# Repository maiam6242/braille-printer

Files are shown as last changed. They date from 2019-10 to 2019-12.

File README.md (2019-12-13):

# Portabraille Printer by Team Dot Dot Dot

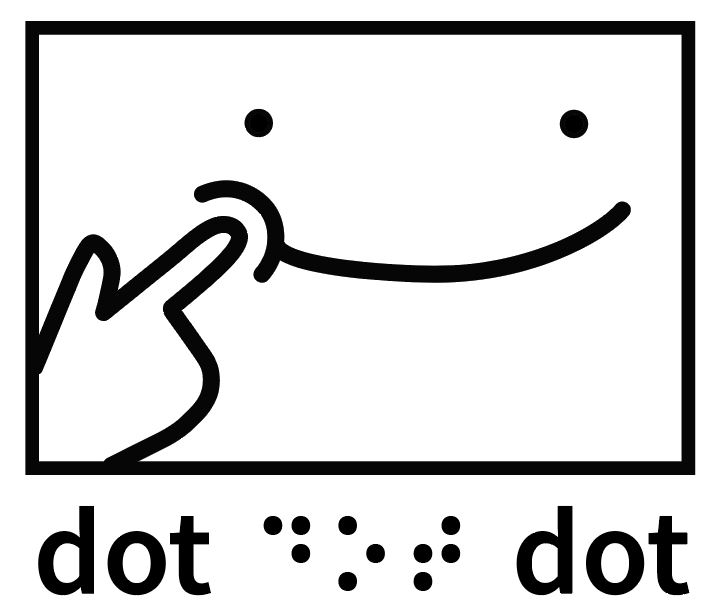
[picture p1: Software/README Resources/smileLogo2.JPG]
Team dot dot dot logo


### The Portabraille Printer is a portable and accessible braille printer which enables users who are visually impaired to quickly and easily produce accurate, high quality braille.

## Table of Contents
- [Introduction](#Introduction "Introduction")
- [This Repository](#This-Repository "This Repository") 
- [Requirements](#Requirements "Requirements")
- [Installation](#Installation "Installation")  
- [Feedback](#Feedback "Feedback") 
- [Team](#Team "Team")  
- [Acknowledgments](#Acknowledgments "Acknowledgments") 

## Introduction
The Portabraille Printer is a device that takes in an English text input, translates that text into uncontracted braille, then prints said braille text on braille paper. It is a low cost product that aims to allow people who are visually impaired to create braille quickly, with applications ranging from producing quick meeting notes to creating accessible promotional materials on the fly. The printer is light, with handles for easy transportation, and has an easy-to-use interface with both braille and English text, creating a user friendly experience for those who are visually impaired or blind. Text documents can be fed to the printer via either the Portabraille Portal on the Portabraille Network or by plugging in a USB. 

## This Repository

This repository contains the vast majority of the files which we created over the course of this project. It is split into two main folders: [Software](https://github.com/maiam6242/braille-printer/tree/master/Software "Software Forlder") and [Firmware](https://github.com/maiam6242/braille-printer/tree/master/Firmware "Firmware Folder"), each of which houses artifacts for the respective subsystems. These folders are also split into multiple subfolders. There is also a [Branding](https://github.com/maiam6242/braille-printer/tree/master/Branding "Branding Folder") folder which has the logo that we used on our shirts.

On the software side, the [Text Side Folder](https://github.com/maiam6242/braille-printer/tree/master/Software/Text%20Side "Text Side Folder") has software that takes a text input, converts it to a braille output and sends it to the firmware. All of this is written in Python. The [Physical Interface Folder](https://github.com/maiam6242/braille-printer/tree/master/Software/Physical%20Interface "Physical Interface Folder") contains software written in Python and designs created in Illustrator which relate to the user interface on our printer. The web interface written in html and designed in Illustrator is in the [Web Interface Folder](https://github.com/maiam6242/braille-printer/tree/master/Software/Web%20Interface "Web Interface Folder"). The [Recognizing Input Folder](https://github.com/maiam6242/braille-printer/tree/master/Software/Recognizing%20Input) includes all of the scripts in bash and Python that allow us to take in USB or Wifi input and the [README Resources Folder](https://github.com/maiam6242/braille-printer/tree/master/Software/README%20Resources "README Resources Folder") contains all of the files referenced in this document. Lastly, the [Startup Scripts Folder](https://github.com/maiam6242/braille-printer/tree/master/Software/StartupScripts "Startup Scripts Folder") contains the scripts which need to be run on the Raspberry Pi to ensure that our software and network run on startup. 

In the firmware folder, the firmware that controls the way paper is loaded and how solenoids act is in the [Arduino Firmware Folder](https://github.com/maiam6242/braille-printer/tree/master/Firmware/Arduino%20Firmware "Arduino Firmware Folder"). All of our firmware is written in C++. The [PCB Folder](https://github.com/maiam6242/braille-printer/tree/master/Firmware/PCB "PCB Folder") contains all of the artifacts from our PCB design.

## Requirements

- Python 3 (or newer)
- Raspberry Pi 3B, 3B+ or 4
- Rasbian Jesse (or newer)

## Installation
The software that runs on the Portabraille Printer has a variety of dependencies. The [startup bash script](https://github.com/maiam6242/braille-printer/blob/master/startup.bash "Startup Bash Script") automatically installs all of the dependencies from all components of our firmware and software. Instructions and code samples for installing these dependencies individually are below. 

#### Python Text to Speech
The following bash command installs pyttsx3, a text to speech library for Python. 
``` bash
pip3 install pyttsx3
```

#### NumPy
The following bash command installs NumPy, a package for computing with Python. 
``` bash
pip3 install numpy
```

#### GPIO Zero
The following bash command installs GPIO Zero, a library for interfacing GPIO devices with Raspberry Pi.
``` bash
pip3 install gpiozero
```

#### PySerial
The following bash command installs pySerial, a module for accessing the serial port.
``` bash
pip3 install pyserial
```

#### eSpeak
The following bash command installs eSpeak, an open source speech synthesizer for Linux and Windows.
```bash
sudo apt-get install espeak
```

#### Flask
The following bash command installs Flask, a microweb framework.
```bash
pip3 install Flask
```

## Feedback
We would love to hear feedback on this project! Feel free to [email us](mailto:mmaterman@olin.edu "mmaterman@olin.edu") or [submit an issue](https://github.com/maiam6242/braille-printer/issues/new/choose "New Issue Request"). If you are interested in contributing to this project or chatting about it in general, please don't hesitate to [email us](mailto:mmaterman@olin.edu "mmaterman@olin.edu") here!

## Team
Annie Tor [@ator1](https://github.com/ator1 "Annie's GitHub")   
Colin Snow [@colinmsnow](https://github.com/colinmsnow "Colin's GitHub")  
Maia Materman [@maiam6242](https://github.com/maiam6242 "Maia's GitHub")  
Megan Ku [@megku4u](https://github.com/megku4u "Megan's GitHub")  
Nathan Weil [@NWeil](https://github.com/NWeil "Nathan's GitHub")  

## Acknowledgments
Thanks to the Fall 2019 Principles of Engineering Teaching Team, Professors Aaron Hoover, Amon Millner, Siddhartan Govindasamy and Stan Reifel for their support and assistance throughout this process. Additional thanks to Frank Ventura, Jerry Berrier, David Kingsbury, John Smith, and Jeanette Kutash and for their INDISPENSABLE help during this adventure. The insights they provided about our design helped us craft a product that is actually usable. Lastly, thank you to the MIT Visually Impaired and Blind User Group for hosting us and letting us pick their brains regarding our printer and braille in general.

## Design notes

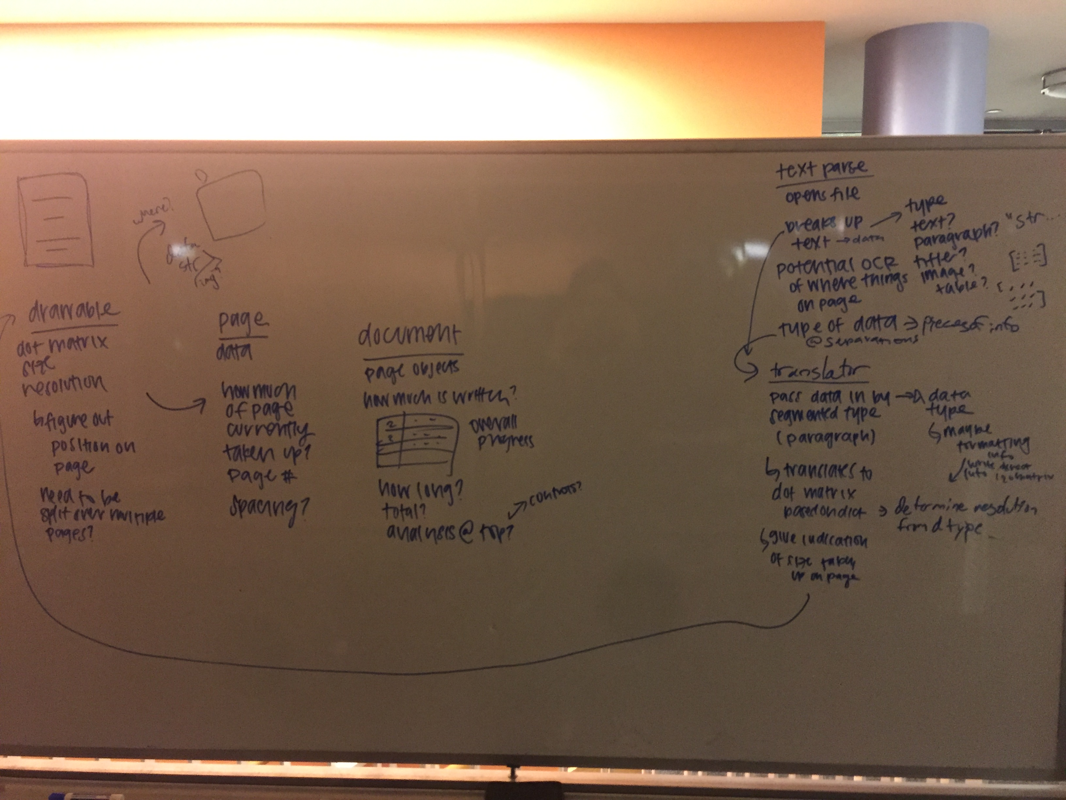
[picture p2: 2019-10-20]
Software/Text_Side/Sprint 1 Inital Code Brainstorm.JPG

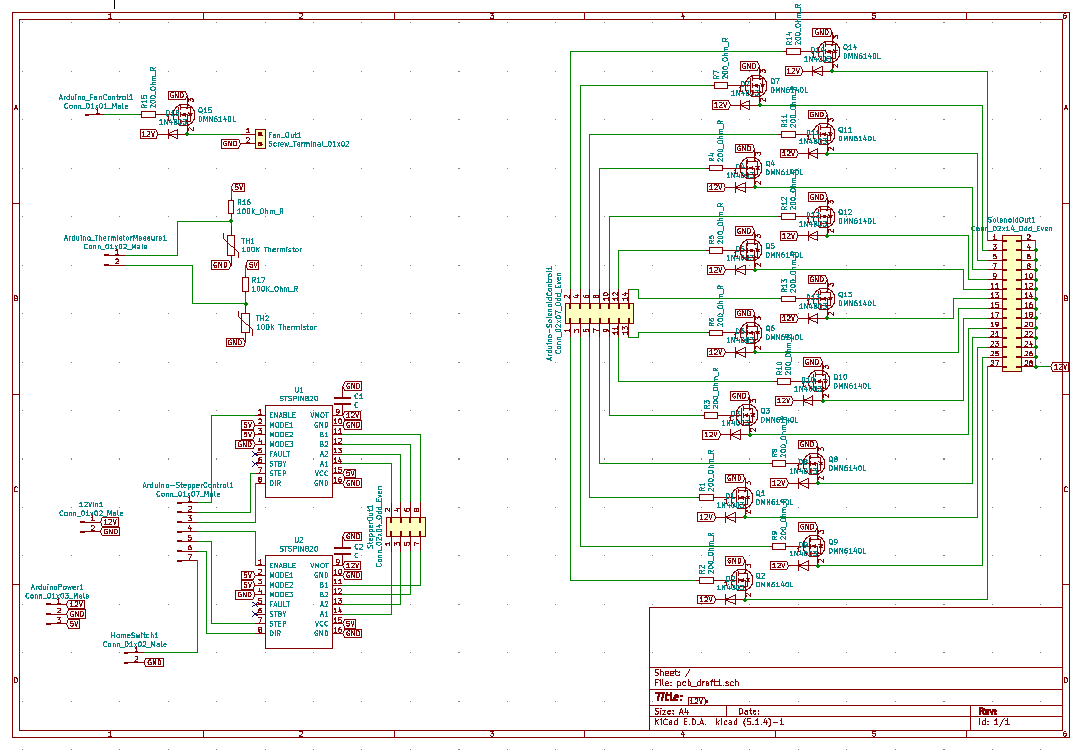
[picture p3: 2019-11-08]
Firmware/PCB/draft1.PNG

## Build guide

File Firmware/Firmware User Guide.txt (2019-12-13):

Firmware User Guide
This guide is intended to describe how the braille firmware works and how it can be used to perform advanced actions.

Overview

The system is built to closely resemble the Gcode standard and shares many common commands with 3D printers. Instructions are sent over serial to the Arduino in the form of a string followed by “\n”. Each command specifies a single action or set of actions for the printer to execute. All commands are currently set to be blocking, which means that the program will not listen for another command until the first command finishes. The program returns information about its interpretation of the command and the resulting action over serial, but this can be disabled with the command M21, which makes it simply return 0 when the last command is completed.

Commands

Movement:

Stepper movement currently operates on a “go-to character” function which assumes that the braille characters are a constant width. They are not a constant width, so that needs to be changed either in the firmware or in python, but it is not really a pressing issue. Movement is split into x and y dimensions, where x is along the width of the paper and y is along its length. There are two commands for movement, G0, and G1, with the only difference being that G1 is half of the speed of G0. They work as follows:

        G0 (axis) (value)  Move the (axis) to the character (value)
                Ex. G0 x 12 moves the x axis to the 12th character
                Ex. G0 y 4 moves the y axis to the fourth character

        G1 (axis) (value)  Same as G0 but at half speed

Solenoids:

The solenoids are controlled with the F command, which takes a sequence of 1s and 0s to denote which solenoid is fired. There is no established order for which solenoid goes where yet so you can decide however you want. The command looks like this:

        F (values[14])  Fire the solenoids with a value of 1
                Ex. F 11111111111111 fires all solenoids
                Ex. F 10000000000000 fires only the first solenoid

Other commands:

There are also a variety of other commands, most of which are made up of the above, to perform other important functions. Steppers should be enabled at the beginning of the program and disabled at the end, and paper loading and x-axis homing should occur for each sheet. For command from Python M21 should be run before all other commands so that the output is consistent. They are as follows:

        G28                     Home (x) axis
        M17                     Enable all steppers
        M18                     Disable all steppers
        M701                    Load paper
        M702                    Unload paper
        M21                     Toggle machine-read mode

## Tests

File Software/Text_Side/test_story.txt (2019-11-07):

Title

“Why in the world do you walk sideways like that?” said a Mother Crab to her son. “You should always walk straight forward with your toes turned out.”

“Show me how to walk, mother dear,” answered the little Crab obediently, “I want to learn.”

So the old Crab tried and tried to walk straight forward. But she could walk sideways only, like her son. And when she wanted to turn her toes out she tripped and fell on her nose.

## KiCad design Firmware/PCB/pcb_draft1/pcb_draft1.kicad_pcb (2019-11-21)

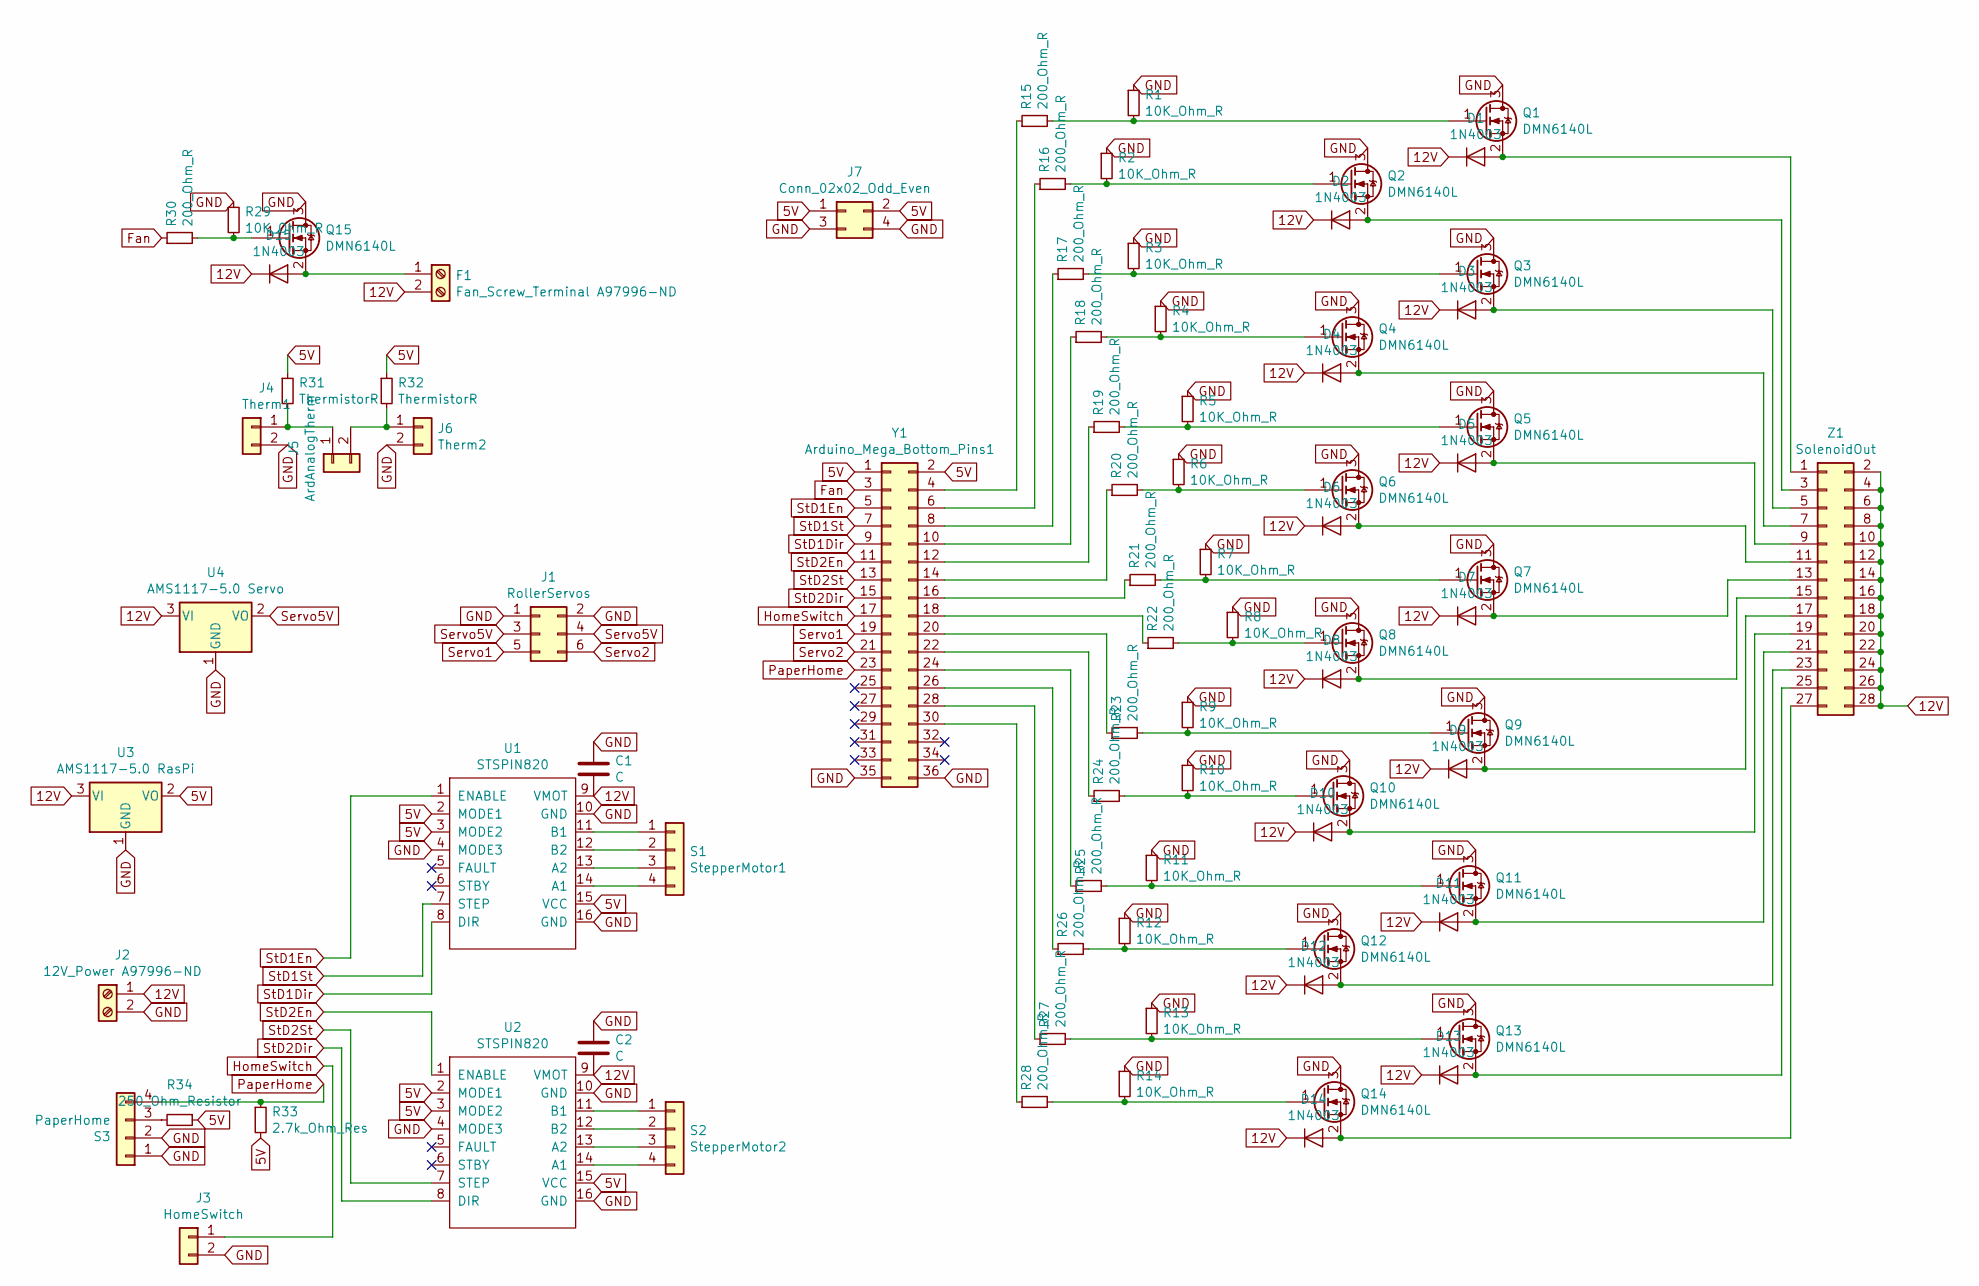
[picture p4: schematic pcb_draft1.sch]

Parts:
C1, C2: C; CP_Radial_D8.0mm_P3.50mm
D1, D2, D3, D4, D5, D6, D7, D8, D9, D10, D11, D12, D13, D14, D15: 1N4003; D_DO-41_SOD81_P10.16mm_Horizontal
F1: Fan_Screw_Terminal A97996-ND; TerminalBlock_Phoenix_MKDS-1,5-2_1x02_P5.00mm_Horizontal
J1: RollerServos; PinHeader_2x03_P2.54mm_Vertical
J2: 12V_Power A97996-ND; TerminalBlock_Phoenix_MKDS-1,5-2_1x02_P5.00mm_Horizontal
J3: HomeSwitch; PinHeader_1x02_P2.54mm_Vertical
J4: Therm1; PinHeader_1x02_P2.54mm_Vertical
J5: ArdAnalogTherm; PinHeader_1x02_P2.54mm_Vertical
J6: Therm2; PinHeader_1x02_P2.54mm_Vertical
J7: Conn_02x02_Odd_Even; PinHeader_2x02_P2.54mm_Vertical
Q1, Q2, Q3, Q4, Q5, Q6, Q7, Q8, Q9, Q10, Q11, Q12, Q13, Q14, Q15: DMN6140L; SOT-223-edited
R1, R2, R3, R4, R5, R6, R7, R8, R9, R10, R11, R12, R13, R14, R29: 10K_Ohm_R; R_0402_1005Metric
R15, R16, R17, R18, R19, R20, R21, R22, R23, R24, R25, R26, R27, R28, R30: 200_Ohm_R; R_0603_1608Metric
R31, R32: ThermistorR; PinHeader_1x02_P2.54mm_Vertical
R33: 2.7k_Ohm_Res; R_0402_1005Metric
R34: 250_Ohm_Resistor; R_0603_1608Metric
S1: StepperMotor1; PinHeader_1x04_P2.54mm_Vertical
S2: StepperMotor2; PinHeader_1x04_P2.54mm_Vertical
S3: PaperHome; PinHeader_1x04_P2.54mm_Vertical
U1, U2: STSPIN820; stepper_driver
U3: AMS1117-5.0 RasPi; SOT-223-3_TabPin2
U4: AMS1117-5.0 Servo; SOT-223-3_TabPin2
Y1: Arduino_Mega_Bottom_Pins1; PinHeader_2x18_P2.54mm_Vertical
Z1: SolenoidOut; PinHeader_2x14_P2.54mm_Vertical

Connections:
5V: J7.1, J7.2, R31.1, R32.1, R33.2, R34.1, U1.2 (MODE1), U1.3 (MODE2), U1.15 (VCC), U2.2 (MODE1), U2.3 (MODE2), U2.15 (VCC), U3.2 (VO), Y1.1, Y1.2
12V: C1.2, C2.2, D1.1 (K), D2.1 (K), D3.1 (K), D4.1 (K), D5.1 (K), D6.1 (K), D7.1 (K), D8.1 (K), D9.1 (K), D10.1 (K), D11.1 (K), D12.1 (K), D13.1 (K), D14.1 (K), D15.1 (K), F1.2, J2.1, U1.9 (VMOT), U2.9 (VMOT), U3.3 (VI), U4.3 (VI), Z1.2, Z1.4, Z1.6, Z1.8, Z1.10, Z1.12, Z1.14, Z1.16, Z1.18, Z1.20, Z1.22, Z1.24, Z1.26, Z1.28
Fan: R30.1, Y1.3
GND: C1.1, C2.1, J1.1, J1.2, J2.2, J3.2, J4.2, J6.2, J7.3, J7.4, Q1.3 (D), Q2.3 (D), Q3.3 (D), Q4.3 (D), Q5.3 (D), Q6.3 (D), Q7.3 (D), Q8.3 (D), Q9.3 (D), Q10.3 (D), Q11.3 (D), Q12.3 (D), Q13.3 (D), Q14.3 (D), Q15.3 (D), R1.1, R2.1, R3.1, R4.1, R5.1, R6.1, R7.1, R8.1, R9.1, R10.1, R11.1, R12.1, R13.1, R14.1, R29.1, S3.1, S3.2, U1.4 (MODE3), U1.10 (GND), U1.16 (GND), U2.4 (MODE3), U2.10 (GND), U2.16 (GND), U3.1 (GND), U4.1 (GND), Y1.35, Y1.36
HomeSwitch: J3.1, Y1.17
unnamed: D1.2 (A), Q1.2 (S), Z1.1
unnamed: D2.2 (A), Q2.2 (S), Z1.3
unnamed: D3.2 (A), Q3.2 (S), Z1.5
unnamed: D4.2 (A), Q4.2 (S), Z1.7
unnamed: D5.2 (A), Q5.2 (S), Z1.9
unnamed: D6.2 (A), Q6.2 (S), Z1.11
unnamed: D7.2 (A), Q7.2 (S), Z1.13
unnamed: D8.2 (A), Q8.2 (S), Z1.15
unnamed: D9.2 (A), Q9.2 (S), Z1.17
unnamed: D10.2 (A), Q10.2 (S), Z1.19
unnamed: D11.2 (A), Q11.2 (S), Z1.21
unnamed: D12.2 (A), Q12.2 (S), Z1.23
unnamed: D13.2 (A), Q13.2 (S), Z1.25
unnamed: D14.2 (A), Q14.2 (S), Z1.27
unnamed: D15.2 (A), F1.1, Q15.2 (S)
unnamed: J4.1, J5.1, R31.2
unnamed: J5.2, J6.1, R32.2
unnamed: Q1.1 (G), R1.2, R15.2
unnamed: Q2.1 (G), R2.2, R16.2
unnamed: Q3.1 (G), R3.2, R17.2
unnamed: Q4.1 (G), R4.2, R18.2
unnamed: Q5.1 (G), R5.2, R19.2
unnamed: Q6.1 (G), R6.2, R20.2
unnamed: Q7.1 (G), R7.2, R21.2
unnamed: Q8.1 (G), R8.2, R22.2
unnamed: Q9.1 (G), R9.2, R23.2
unnamed: Q10.1 (G), R10.2, R24.2
unnamed: Q11.1 (G), R11.2, R25.2
unnamed: Q12.1 (G), R12.2, R26.2
unnamed: Q13.1 (G), R13.2, R27.2
unnamed: Q14.1 (G), R14.2, R28.2
unnamed: Q15.1 (G), R29.2, R30.2
unnamed: R15.1, Y1.4
unnamed: R16.1, Y1.6
unnamed: R17.1, Y1.8
unnamed: R18.1, Y1.10
unnamed: R19.1, Y1.12
unnamed: R20.1, Y1.14
unnamed: R21.1, Y1.16
unnamed: R22.1, Y1.18
unnamed: R23.1, Y1.20
unnamed: R24.1, Y1.22
unnamed: R25.1, Y1.24
unnamed: R26.1, Y1.26
unnamed: R27.1, Y1.28
unnamed: R28.1, Y1.30
unnamed: R34.2, S3.3
unnamed: S1.1, U1.11 (B1)
unnamed: S1.2, U1.12 (B2)
unnamed: S1.3, U1.13 (A2)
unnamed: S1.4, U1.14 (A1)
unnamed: S2.1, U2.11 (B1)
unnamed: S2.2, U2.12 (B2)
unnamed: S2.3, U2.13 (A2)
unnamed: S2.4, U2.14 (A1)
PaperHome: R33.1, S3.4, Y1.23
Servo1: J1.5, Y1.19
Servo2: J1.6, Y1.21
Servo5V: J1.3, J1.4, U4.2 (VO)
StD1Dir: U1.8 (DIR), Y1.9
StD1En: U1.1 (ENABLE), Y1.5
StD1St: U1.7 (STEP), Y1.7
StD2Dir: U2.8 (DIR), Y1.15
StD2En: U2.1 (ENABLE), Y1.11
StD2St: U2.7 (STEP), Y1.13

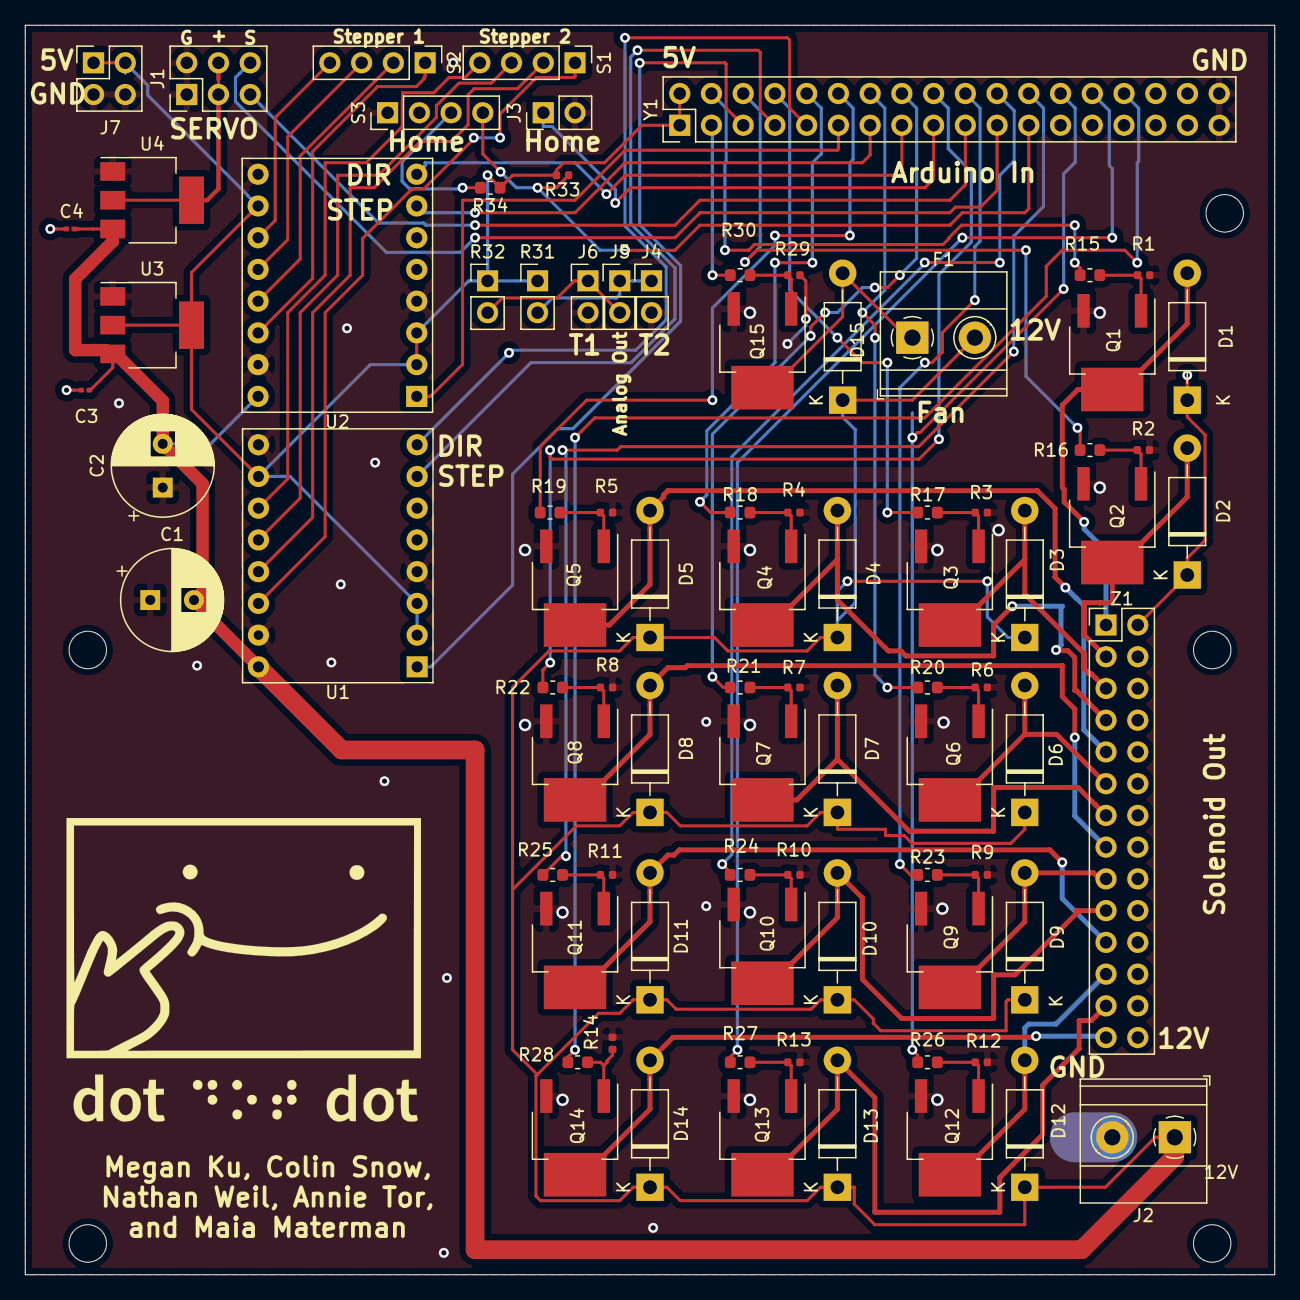
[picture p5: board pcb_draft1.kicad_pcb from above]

Board: 2 copper layers, 100.0 x 100.0 mm, 86 parts (0 on the bottom side), 70 nets.

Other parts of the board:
12V: MountingHole_3mm
C3, C4: C_0201_0603Metric

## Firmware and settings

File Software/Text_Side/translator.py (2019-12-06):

#coding=utf-8
'''Translates text into braille'''

import numpy as np
#TODO: Add single opening and closing quotation marks...
# also figure out if this is already done, oof


# page = page
CHARACTERS_PER_LINE = 28
SYMBOLS = {'a' : np.array([[1, 0], [0, 0], [0, 0]]),
           'b' : np.array([[1, 0], [1, 0], [0, 0]]),
           'c' : np.array([[1, 1], [0, 0], [0, 0]]),
           'd' : np.array([[1, 1], [0, 1], [0, 0]]),
           'e' : np.array([[1, 0], [0, 1], [0, 0]]),
           'f' : np.array([[1, 1], [1, 0], [0, 0]]),
           'g' : np.array([[1, 1], [1, 1], [0, 0]]),
           'h' : np.array([[1, 0], [1, 1], [0, 0]]),
           'i' : np.array([[0, 1], [1, 0], [0, 0]]),
           'j' : np.array([[0, 1], [1, 1], [0, 0]]),
           'k' : np.array([[1, 0], [0, 0], [1, 0]]),
           'l' : np.array([[1, 0], [1, 0], [1, 0]]),
           'm' : np.array([[1, 1], [0, 0], [1, 0]]),
           'n' : np.array([[1, 1], [0, 1], [1, 0]]),
           'o' : np.array([[1, 0], [0, 1], [1, 0]]),
           'p' : np.array([[1, 1], [1, 0], [1, 0]]),
           'q' : np.array([[1, 1], [1, 1], [1, 0]]),
           'r' : np.array([[1, 0], [1, 1], [1, 0]]),
           's' : np.array([[0, 1], [1, 0], [1, 0]]),
           't' : np.array([[0, 1], [1, 1], [1, 0]]),
           'u' : np.array([[1, 0], [0, 0], [1, 1]]),
           'v' : np.array([[1, 0], [1, 0], [1, 1]]),
           'w' : np.array([[0, 1], [1, 1], [0, 1]]),
           'x' : np.array([[1, 1], [0, 0], [1, 1]]),
           'y' : np.array([[1, 1], [0, 1], [1, 1]]),
           'z' : np.array([[1, 0], [0, 1], [1, 1]]),
           '1' : np.array([[1, 0], [0, 0], [0, 0]]),
           '2' : np.array([[1, 0], [1, 0], [0, 0]]),
           '3' : np.array([[1, 1], [0, 0], [0, 0]]),
           '4' : np.array([[1, 1], [0, 1], [0, 0]]),
           '5' : np.array([[1, 0], [0, 1], [0, 0]]),
           '6' : np.array([[1, 1], [1, 0], [0, 0]]),
           '7' : np.array([[1, 1], [1, 1], [0, 0]]),
           '8' : np.array([[1, 0], [1, 1], [0, 0]]),
           '9' : np.array([[0, 1], [1, 0], [0, 0]]),
           '0' : np.array([[0, 1], [1, 1], [0, 0]]),
           ' ' : np.array([[0, 0], [0, 0], [0, 0]]),
           ',' : np.array([[0, 0], [1, 0], [0, 0]]),
           ';' : np.array([[0, 0], [1, 0], [1, 0]]),
           ':' : np.array([[0, 0], [1, 1], [0, 0]]),
           '.' : np.array([[0, 0], [1, 1], [0, 1]]),
           '!' : np.array([[0, 0], [1, 1], [1, 0]]),
           "'" : np.array([[0, 0], [0, 0], [1, 0]]),
           '-' : np.array([[0, 0], [0, 0], [1, 1]]),
           '?' : np.array([[0, 0], [1, 0], [1, 1]]),
           '#' : np.array([[0, 1], [0, 1], [1, 1]]),
           '(' : np.array([[0, 0], [1, 1], [1, 1]]),
           ')' : np.array([[0, 0], [1, 1], [1, 1]]),
           'Ξ' : np.array([[0, 1], [0, 1], [1, 1]]),
           '“' : np.array([[0, 0], [1, 0], [1, 1]]),
           '”' : np.array([[0, 0], [0, 1], [1, 1]]),
           'opening "' : np.array([[0, 0], [1, 0], [1, 1]]),
           'closing "' : np.array([[0, 0], [0, 1], [1, 1]]),
           'ζ' : np.array([[0, 0], [0, 0], [0, 1]]),
           'η' : np.array([[0, 0, 0, 0], [0, 0, 0, 0],
                           [0, 1, 0, 1]]),
           '_' : np.array([[0, 1, 0, 0], [0, 0, 0, 0],
                           [0, 1, 1, 1]]),
           '[' : np.array([[0, 1, 1, 0], [0, 0, 1, 0],
                           [0, 1, 0, 1]]),
           ']' : np.array([[0, 1, 0, 1], [0, 0, 0, 1],
                           [0, 1, 1, 0]]),
           '*' : np.array([[0, 0, 0, 0], [0, 1, 0, 1],
                           [0, 0, 1, 0]]),
           '$' : np.array([[0, 1, 0, 1], [0, 0, 1, 0],
                           [0, 0, 1, 0]])
           }

class Translator:
    '''Translates text to braille'''

    def __init__(self, interface):
        self.interface = interface

    OPEN_QUOTE = False
    size = []

    def convert_to_braille(self, segment):
        '''
        Converts the entirety of the segment into a dot matrix based
        on the'SYMBOLS' dictionary in this class
        Args: the whole segment in english
        Returns: the whole segment in braille
        '''
        braille_text = []
        if not self.is_new_line(segment):
            print(segment)
            segment = self.find_caps(segment)
            segment = self.find_nums(segment)
            segment = str.lower(str(segment))
            for char in segment:
                self.interface.check_buttons()
                char_trans = self.translate_text(char)
                braille_text.append(char_trans)
            braille_text, num_lines = self.split_into_lines(braille_text)
        else:
            braille_text = self.make_new_line()
            num_lines = 1
        # print(braille_text)

        return braille_text, num_lines

    def is_new_line(self, segment):
        '''
        Determines whether or not the segment is a new line character (ie paragraph break)
        Args: The original english segment
        Returns: True if the segment is a new line character, False if it is not
        '''
        if segment == '\n':
            return True
        else:
            return False

    def make_new_line(self):
        '''
        Creates a new line of braille text (row of spaces)
        Returns: A numpy array that is equal to a row of spaces (24/30 spaces) in braille
        '''

        return SYMBOLS[' ']*CHARACTERS_PER_LINE

    def find_caps(self, segment):
        '''
        Finds every capital letter or word and inserts the corresponding characters in braille
        Args: segment in English
        Returns: The segment in English with a weird symbol
        (non-english)characters interspersed to denote capitalization
        i.e. MAIA -> ||MAIA  or Maia -> | Maia

        # >>> find_caps('HELLO')
        # 'ηHELLO'
        # >>> find_caps('Hello')
        # 'ζHello'
        # >>> find_caps('HI THERE I am wondering what You think About this wacky STRING')
        # 'ηHI ηTHERE ζI am wondering what ζYou think ζAbout this wacky ηSTRING'
        # >>> find_caps('HEy! This is super COOOL! Cool cool CooL! HOw do you feeEEEEl?')
        # 'ηHEy! ζThis is super ηCOOOL! ζCool cool ζCooζL! ηHOw do you feeηEEEEl?'
        '''
        #TODO: Whatever you make this letter(s) associate it with the cap letter and
        # cap word things in the dictionary, so that the translate_text
        # function can recognize everything
        #TODO: Talk to real people about how capitals work so we can handle them better
        # Notes:
            #  For some reason setting newlist_segment = list_segment causes them both to
            # be changed when one is so adding list() fixes this for reasons I don't understand
            # islower() and isupper() both return false if the string is a space so you
            #  need to use not isupper() which is super annoying but works

        list_segment = list(segment)
        newlist_segment = list(list_segment)
        offset = 0
        for i, _ in enumerate(list_segment):
            self.interface.check_buttons()

            if i == 0:
                lastupper = False # If there is no character
                            #before it tell it that the last character was not uppercase
            else:
                lastupper = list_segment[i-1].isupper()

            if list_segment[i].isupper():
                if i < len(list_segment) -1 and list_segment[i+1].isupper() and not lastupper:
                    newlist_segment.insert(i+offset, 'η')
                    offset += 1
                else:
                    if not lastupper:
                        newlist_segment.insert(i+offset, 'ζ')
                        offset += 1


        output_string = ''
        return output_string.join(newlist_segment)

    def find_nums(self, segment):
        '''
        Finds every number in the string and adds a
        Args: segment in English
        Returns: The segment in English with a weird symbol
        (non-english)characters interspersed to denote capitalization
        i.e. MAIA -> ||MAIA  or Maia -> | Maia

        # >>> find_nums('1 2 3')
        # 'Ξ1 Ξ2 Ξ3'
        # >>> find_nums('123')
        # 'Ξ123'
        # >>> find_nums('The numbers are 1 and 123 and 35,245')
        # 'The numbers are Ξ1 and Ξ123 and Ξ35245'

        '''
        # Notes:
            #  For some reason setting newlist_segment = list_segment
            # causes them both to be changed when one is so adding list()
            # fixes this for reasons I don't understand

        list_segment = list(segment)
        i = 0
        while i < len(list_segment):   # This is needed for numbers
            self.interface.check_buttons()

                                    #with a comma in them to prevent it from being two numbers
            if list_segment[i] == ',':
                if list_segment[i-1].isnumeric() and list_segment[i+1].isnumeric():
                    list_segment.pop(i)
            i += 1

        newlist_segment = list(list_segment)
        offset = 0
        for i, _ in enumerate(list_segment):
            self.interface.check_buttons()

            if i == 0:
                lastupper = False # If there is no character
                                #before it tell it that the last character was not uppercase
            else:
                lastupper = list_segment[i-1].isnumeric()

            if list_segment[i].isnumeric():
                if i< len(list_segment) -1 and list_segment[i+1].isnumeric() and not lastupper:
                    newlist_segment.insert(i+offset,'Ξ')
                    offset += 1
                else:
                    if not lastupper:
                        newlist_segment.insert(i+offset, 'Ξ')
                        offset += 1

        output_string = ''

        return output_string.join(newlist_segment)

    def translate_text(self, char):
        '''
        Converts a single character into braille based on "SYMBOLS"; 
        handles more of the syntactical things and other rules with Braille
        Args: A single English character
        Returns: A single Braille character

        # >>> translate_text('"')
        # array([[0, 0],
        #     [1, 0],
        #     [1, 1]])
        # >>> translate_text('"')
        # array([[0, 0],
        #     [0, 1],
        #     [1, 1]])
        # >>> translate_text('>')
        # character wasn't found
        # array([[0, 0],
        #     [1, 0],
        #     [1, 1]])
        # >>> translate_text('l')
        # array([[1, 0],
        #     [1, 0],
        #     [1, 0]])
        '''
        
        global OPEN_QUOTE
        # print(char)
        if char == '"':
            if not OPEN_QUOTE:
                OPEN_QUOTE = True
                return SYMBOLS['opening "']
            else:
                OPEN_QUOTE = False
                return SYMBOLS['closing "']
        else:
            try:
                # print(SYMBOLS[char])
                return SYMBOLS[char]
            except:   #FIXME: Figure what error is being excepted
                print('character wasn\'t found')
                return SYMBOLS['?']

    def split_into_lines(self, braille_segment):
        '''
        Takes the segment and splits it into 24? 30? character lines
        Args: Entire segment in braille (as a list of numpy arrays)
        Returns: A numpy array that is a segment (size is twice the number of characters per line)

        # >>> test_array = [np.array([[1, 0], [1, 0], [1, 0]]),np.array([[1, 0], [1, 0], [1, 0]]),
        # np.array([[1, 0], [1, 0], [1, 0]]),np.array([[1, 0], [1, 0], [1, 0]]),np.array([[1, 0], 
        # [1, 0], [1, 0]]),np.array([[1, 0], [1, 0], [1, 0]]),np.array([[1, 0], [1, 0], [1, 0]]),
        # np.array([[1, 0], [1, 0], [1, 0]]),np.array([[1, 0], [1, 0], [1, 0]]),np.array([[1, 0], 
        # [1, 0], [1, 0]])]
        # >>> test_array_2 = [np.array([[1, 0], [1, 0], [1, 0]]),np.array([[1, 0], [1, 0], [1, 0]]),
        # np.array([[1, 0], [1, 0], [1, 0]]),np.array([[1, 0], [1, 0], [1, 0]]),np.array([[1, 0], 
        # [1, 0], [1, 0]]),np.array([[1, 0], [1, 0], [1, 0]]),np.array([[1, 0], [1, 0], [1, 0]]),
        # np.array([[1, 0], [1, 0], [1, 0]]),np.array([[1, 0], [1, 0], [1, 0]]),np.array([[1, 0], 
        # [1, 0], [1, 0]]),np.array([[1, 0], [1, 0], [1, 0]]),np.array([[1, 0], [1, 0], [1, 0]]),
        # np.array([[1, 0], [1, 0], [1, 0]]),np.array([[1, 0], [1, 0], [1, 0]]),np.array([[1, 0], 
        # [1, 0], [1, 0]]),np.array([[1, 0], [1, 0], [1, 0]]),np.array([[1, 0], [1, 0], [1, 0]]),
        # np.array([[1, 0], [1, 0], [1, 0]]),np.array([[1, 0], [1, 0], [1, 0]]),np.array([[1, 0], 
        # [1, 0], [1, 0]]),np.array([[1, 0], [1, 0], [1, 0]]),np.array([[1, 0], [1, 0], [1, 0]]),
        # np.array([[1, 0], [1, 0], [1, 0]]),np.array([[1, 0], [1, 0], [1, 0]]),np.array([[1, 0], 
        # [1, 0], [1, 0]]),np.array([[1, 0], [1, 0], [1, 0]]),np.array([[1, 0], [1, 0], [1, 0]]),
        # np.array([[1, 0], [1, 0], [1, 0]]),np.array([[1, 0], [1, 0], [1, 0]]),np.array([[1, 0], 
        # [1, 0], [1, 0]]),np.array([[1, 0], [1, 0], [1, 0]]),np.array([[1, 0], [1, 0], [1, 0]]),
        # np.array([[1, 0], [1, 0], [1, 0]]),np.array([[1, 0], [1, 0], [1, 0]]),np.array([[1, 0], 
        # [1, 0], [1, 0]]),np.array([[1, 0], [1, 0], [1, 0]]),np.array([[1, 0], [1, 0], [1, 0]]),
        # np.array([[1, 0], [1, 0], [1, 0]]),np.array([[1, 0], [1, 0], [1, 0]]),np.array([[1, 0],
        #  [1, 0], [1, 0]]),np.array([[1, 0], [1, 0], [1, 0]]),np.array([[1, 0], [1, 0], [1, 0]]),
        # np.array([[1, 0], [1, 0], [1, 0]]),np.array([[1, 0], [1, 0], [1, 0]]),np.array([[1, 0],
        #  [1, 0], [1, 0]]),np.array([[1, 0], [1, 0], [1, 0]]),np.array([[1, 0], [1, 0], [1, 0]]),
        # np.array([[1, 0], [1, 0], [1, 0]]),np.array([[1, 0], [1, 0], [1, 0]]),np.array([[1, 0],
        #  [1, 0], [1, 0]]),np.array([[1, 0], [1, 0], [1, 0]]),np.array([[1, 0], [1, 0], [1, 0]]),
        # np.array([[1, 0], [1, 0], [1, 0]]),np.array([[1, 0], [1, 0], [1, 0]]),np.array([[1, 0],
        #  [1, 0], [1, 0]]),np.array([[1, 0], [1, 0], [1, 0]]),np.array([[1, 0], [1, 0], [1, 0]]),
        # np.array([[1, 0], [1, 0], [1, 0]]),np.array([[1, 0], [1, 0], [1, 0]]),np.array([[1, 0],
        #  [1, 0], [1, 0]])]
        # >>> split_into_lines(test_array)
        # array([[1., 0., 1., 0., 1., 0., 1., 0., 1., 0., 1., 0., 1., 0., 1., 0.,
        #         1., 0., 1., 0., 0., 0., 0., 0., 0., 0., 0., 0., 0., 0., 0., 0.,
        #         0., 0., 0., 0., 0., 0., 0., 0., 0., 0., 0., 0., 0., 0., 0., 0.,
        #         0., 0., 0., 0., 0., 0., 0., 0., 0., 0., 0., 0.],
        #     [1., 0., 1., 0., 1., 0., 1., 0., 1., 0., 1., 0., 1., 0., 1., 0.,
        #         1., 0., 1., 0., 0., 0., 0., 0., 0., 0., 0., 0., 0., 0., 0., 0.,
        #         0., 0., 0., 0., 0., 0., 0., 0., 0., 0., 0., 0., 0., 0., 0., 0.,
        #         0., 0., 0., 0., 0., 0., 0., 0., 0., 0., 0., 0.],
        #     [1., 0., 1., 0., 1., 0., 1., 0., 1., 0., 1., 0., 1., 0., 1., 0.,
        #         1., 0., 1., 0., 0., 0., 0., 0., 0., 0., 0., 0., 0., 0., 0., 0.,
        #         0., 0., 0., 0., 0., 0., 0., 0., 0., 0., 0., 0., 0., 0., 0., 0.,
        #         0., 0., 0., 0., 0., 0., 0., 0., 0., 0., 0., 0.]])
        # >>> split_into_lines(test_array_2)
        # array([[1., 0., 1., 0., 1., 0., 1., 0., 1., 0, 1, 0, 1, 0., 1., 0.,
        #         1., 0., 1., 0., 1., 0., 1., 0., 1., 0., 1., 0., 1., 0., 1., 0.,
        #         1., 0., 1., 0., 1., 0., 1., 0., 1., 0., 1., 0., 1., 0., 1., 0.,
        #         1., 0., 1., 0., 1., 0., 1., 0., 1., 0., 1., 0.],
        #     [1., 0., 1., 0., 1., 0., 1., 0., 1., 0., 1., 0., 1., 0., 1., 0.,
        #         1., 0., 1., 0., 1., 0., 1., 0., 1., 0., 1., 0., 1., 0., 1., 0.,
        #         1., 0., 1., 0., 1., 0., 1., 0., 1., 0., 1., 0., 1., 0., 1., 0.,
        #         1., 0., 1., 0., 1., 0., 1., 0., 1., 0., 1., 0.],
        #     [1., 0., 1., 0., 1., 0., 1., 0., 1., 0., 1., 0., 1., 0., 1., 0.,
        #         1., 0., 1., 0., 1., 0., 1., 0., 1., 0., 1., 0., 1., 0., 1., 0.,
        #         1., 0., 1., 0., 1., 0., 1., 0., 1., 0., 1., 0., 1., 0., 1., 0.,
        #         1., 0., 1., 0., 1., 0., 1., 0., 1., 0., 1., 0.],
        #     [1., 0., 1., 0., 1., 0., 1., 0., 1., 0., 1., 0., 1., 0., 1., 0.,
        #         1., 0., 1., 0., 1., 0., 1., 0., 1., 0., 1., 0., 1., 0., 1., 0.,
        #         1., 0., 1., 0., 1., 0., 1., 0., 1., 0., 1., 0., 1., 0., 1., 0.,
        #         1., 0., 1., 0., 1., 0., 1., 0., 1., 0., 0., 0.],
        #     [1., 0., 1., 0., 1., 0., 1., 0., 1., 0., 1., 0., 1., 0., 1., 0.,
        #         1., 0., 1., 0., 1., 0., 1., 0., 1., 0., 1., 0., 1., 0., 1., 0.,
        #         1., 0., 1., 0., 1., 0., 1., 0., 1., 0., 1., 0., 1., 0., 1., 0.,
        #         1., 0., 1., 0., 1., 0., 1., 0., 1., 0., 0., 0.],
        #     [1., 0., 1., 0., 1., 0., 1., 0., 1., 0., 1., 0., 1., 0., 1., 0.,
        #         1., 0., 1., 0., 1., 0., 1., 0., 1., 0., 1., 0., 1., 0., 1., 0.,
        #         1., 0., 1., 0., 1., 0., 1., 0., 1., 0., 1., 0., 1., 0., 1., 0.,
        #         1., 0., 1., 0., 1., 0., 1., 0., 1., 0., 0., 0.]])
        '''
        current_line = []
        lines = []
        characters_in_line = 0
        space = np.array([[0, 0], [0, 0], [0, 0]])

        for character in braille_segment:
            self.interface.check_buttons()

            if np.size(character, 0) == 4:
                character_size = 2
            else:
                character_size = 1
            if character_size + characters_in_line <= CHARACTERS_PER_LINE:
                current_line.append(character)
                characters_in_line += character_size
            else:
                lines.append(current_line)
                current_line = []
                characters_in_line = 0
        lines.append(current_line)

        line_arrays = []

        for line in lines:
            self.interface.check_buttons()


            line_length = np.shape(line)[0]
            print(line_length)
            line_array = []
            if CHARACTERS_PER_LINE - line_length != 0:
                spaces = []

                for _ in range(0, (CHARACTERS_PER_LINE - line_length)):
                    spaces.append(space)

                if np.size(line) != 0:
                    line_array = np.concatenate((np.asarray(line), np.asarray(spaces)), axis=0)
                else:
                    line_array = np.asarray(spaces)
            if not len(line_array):
                line_arrays.append([line])
            else:
                line_arrays.append([line_array])

        output_array = np.vstack(np.asarray(line_arrays))
        num_lines = len(lines)
        print(type(output_array))

        return output_array, num_lines


if __name__ == '__main__':
    import doctest
    # doctest.run_docstring_examples(split_into_lines, globals())
    doctest.testmod()
    TRANS = Translator()
    TRANS.convert_to_braille('“Yay Braille!”')

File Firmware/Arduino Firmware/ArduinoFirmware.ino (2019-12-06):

// Firmware for Braille Printer on Arduino
// Created by Colin Snow on 10/27/19

#include "Steppers-2.h"
#include <AccelStepper.h>
#include "Solenoid.h"
#include "GcodeInterpreter.h"

void setup(){
    Serial.begin(115200); 
}

void loop(){

    // int selectedPins[] = {23,25,27,29,31,33,35,37,39,41,43,45,47,49};
    // int selectedPins[] = {37,41,39,47,49,45,43,31,23,35,33,27,25,29};
    int selectedPins[] = {33,35,31,29,27,25,23,49,45,47,43,41,39,37};
    // int selectedPins[] = {2,3,4,5,6,7,35,37,39,41,43,45,47,49};
    Solenoid solenoid;
    solenoid.setPins(selectedPins);
    HorizontalStepper horizontalStepper(26, 28, 24, 36, 2000, 8000);
    PaperStepper paperStepper(32,34,30,42, 200, 8000);
    GcodeInterpreter interpreter;

    while (1){
        interpreter.executeCommand(horizontalStepper, paperStepper, solenoid);
    }
}

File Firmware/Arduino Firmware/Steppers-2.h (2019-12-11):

#include <SoftwareSerial.h>

// Stepper control module v2
// Created by Colin Snow on 10/29/19

#include <AccelStepper.h>

// A stepper object which has added functionality for moving to characters and homing
class HorizontalStepper :  public AccelStepper {

    protected:
        int homePin;
        double stepsPermm = 42. * 100. / 104.25 * 100. / 100.84; // How many steps it needs to move to move one mm  2000 * 8 / Pi * d (12 mm)
        int stepsToFirstCharacter = 60; // Steps needed to get to origin
        int absolutePosition = 0 ;
        int enablePin;

    public:
        HorizontalStepper (int step, int direction, int enable, int home_pin, int maxSpeed, int accel) : AccelStepper(1, step, direction){
            homePin = home_pin;
            pinMode(homePin, INPUT_PULLUP);
            // setEnablePin(enable);
            enablePin = enable;
            // setPinsInverted(false,false,true);
            setMaxSpeed(double(maxSpeed));
            setAcceleration(double(accel));
        }

        // Moves the stepper to the specified character
        // @param desiredCharacter The character to go to
        // @param stepsPerSecond The speed of the motor in steps/second
        void goTomm(double desiredCharacter, int speed){
            double desiredPosition = double(desiredCharacter) * stepsPermm;
            setMaxSpeed(double(speed));
            runToNewPosition(int(desiredPosition));
        }

        // Homes the horizontal axis
        void home(int speed){
            enable();
            setMaxSpeed(speed);
            while (digitalRead(homePin)){
                int position = currentPosition();
                runToNewPosition(position -20);
            }
            setMaxSpeed(speed / 2);
            int position = currentPosition();
            runToNewPosition(position + 40);
            while (digitalRead(homePin)){
                int position = currentPosition();
                runToNewPosition(position -1);
            }
            setCurrentPosition(0);
            runToNewPosition(stepsToFirstCharacter);
            goTomm(45.1, 8000);
            setCurrentPosition(0);
        }

        void enable(){
            digitalWrite(enablePin, LOW);
        }
        void disable(){
            digitalWrite(enablePin, HIGH);
        }
        double currentmm(){
            return currentPosition() / stepsPermm;
        }
};

// A stepper object which handles paper controls such as going to character and loading
class PaperStepper : public AccelStepper{

    protected:
    int loadSteps = 225; // Number of steps needed to load in Paper
    int unloadSteps = 3000; // Number of steps needed to unload Paper
    int stepsPermm = 40; // Number of steps to move up one mm 2000 * 8 / Pi * d (12.7 mm)
    int enablePin;
    int homePin;

    public:

        PaperStepper (int step, int direction, int enable, int home,  int maxSpeed, int accel) : AccelStepper(1, step, direction){
            // setEnablePin(enable);
            enablePin = enable;
            homePin = home;
            pinMode(homePin, INPUT);
            // setPinsInverted(false,false,true);
            setMaxSpeed(maxSpeed);
            setAcceleration(accel);
            setPinsInverted(true,false,false);
        }

        // Loads paper into the machine
        // @params stepsPerSecond The motor speed in steps/second
        // void load(int speed){
        //     setCurrentPosition(0);
        //     setMaxSpeed(speed);
        //     runToNewPosition(loadSteps);
        //     setCurrentPosition(0);
        // }
        void load(int speed){
            enable();
            setMaxSpeed(speed);
            while (!digitalRead(homePin)){
                int position = currentPosition();
                runToNewPosition(position +20);
            }
            setMaxSpeed(speed / 2);
            int position = currentPosition();
            runToNewPosition(position - 40);
            while (!digitalRead(homePin)){
                int position = currentPosition();
                runToNewPosition(position +1);
            }
            setCurrentPosition(0);
            goTomm(-27, 8000);
            setCurrentPosition(0);
        }

        // Unloads paper from the machine
        // @params stepsPerSecond The motor speed in steps/second
        void unload(int speed){
            int position = currentPosition();
            setMaxSpeed(speed);
            runToNewPosition(position + unloadSteps);
        }

        // Moves the stepper to the specified character
        // @param desiredCharacter The character to go to
        // @param stepsPerSecond The speed of the motor in steps/second
        void goTomm(double desiredCharacter, int speed){
            double desiredPosition = desiredCharacter * stepsPermm;
            setMaxSpeed(speed);
            runToNewPosition(desiredPosition);
        }
        void enable(){
            digitalWrite(enablePin, LOW);
        }
        void disable(){
            digitalWrite(enablePin, HIGH);
        }
        double currentmm(){
            return currentPosition() / stepsPermm;
        }
};

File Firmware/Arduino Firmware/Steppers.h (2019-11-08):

// Stepper control module
// Created by Colin Snow on 10/27/19
// Depreciated

// Base class for controlling stepper motors
class Stepper{

    protected:

        int stepPin;
        int directionPin;
        int enablePin;
        int position;

    public:

        // getters and setters

        int getPosition() {return position;}
        void setPosition(int value) {position = value;}
        int getStepPin() {return stepPin;}
        void setStepPin(int value) {stepPin = value;}
        int getDirectionPin() {return directionPin;}
        void setDirectionPin(int value) {directionPin = value;}
        int getEnablePin() {return enablePin;}
        void setEnablePin(int value) {enablePin = value;}

        // Activates stepper
        void activate(){digitalWrite(enablePin, LOW);}
        // Deactivates stepper
        void deactivate(){digitalWrite(enablePin, HIGH);}


        // Steps the stepper once
        void stepOnce(){
            digitalWrite(stepPin, HIGH);
            digitalWrite(stepPin, LOW);
        }

        // Moves the stepper the specified number of steps at the given speed
        // @param steps Number of steps to move
        // @param stepsPerSecond The speed of the motor in steps/second
        void step(int steps, int stepsPerSecond){

            if (steps >= 0){digitalWrite(directionPin, HIGH);}
            if (steps < 0){digitalWrite(directionPin, LOW);}

            for (int i = 1; i<abs(steps); i++){

                stepOnce();
                delay(1000 / stepsPerSecond);
            }
            position += steps;
        }

        // Moves the stepper to an absolute position
        // @param targetPosition The position to move to
        // @param stepsPerSecond The speed of the motor in steps/second
        void goTo(int targetPosition, int stepsPerSecond){

            int stepsToGo = targetPosition - position;
            step(stepsToGo, stepsPerSecond);
        }

};

// A stepper object which has added functionality for moving to characters and homing
class HorizontalStepper :  public Stepper {

    protected:
        int homePin;
        int stepsPerCharacter = 20; // How many steps it needs to move to move one character over
        int stepsToFirstCharacter = 30; // Steps needed to get to origin

    public:

        void setPins(int step_pin, int direction_pin, int enable_pin, int home_pin){
            stepPin = step_pin;
            directionPin = direction_pin;
            enablePin = enable_pin;
            homePin = home_pin;
            pinMode(stepPin, OUTPUT);
            pinMode(directionPin,OUTPUT);
            pinMode(enablePin,OUTPUT);
            pinMode(homePin,INPUT);
        }

        // Homes the horizontal axis
        void home(){

            activate();

            digitalWrite(directionPin, LOW);

            while (! digitalRead(homePin)){
                stepOnce();
                delay(1000/30);
            }

            step(30, 10);

            digitalWrite(directionPin, LOW);

            while (! digitalRead(homePin)){
                stepOnce();
                delay(1000/10);
            }

            step(stepsToFirstCharacter, 10);

            position = 0;

            deactivate();
        }

        // Moves the stepper to the specified character
        // @param desiredCharacter The character to go to
        // @param stepsPerSecond The speed of the motor in steps/second
        void goToCharacter(int desiredCharacter, int stepsPerSecond){

            int desiredPosition = desiredCharacter * stepsPerCharacter;

            goTo(desiredPosition, stepsPerSecond);
        }
};

// A stepper object which handles paper controls such as going to character and loading
class PaperStepper : public Stepper{

    protected:
    int loadSteps = 50; // Number of steps needed to load in Paper
    int unloadSteps = 100; // Number of steps needed to unload Paper
    int stepsPerCharacter = 40; // Number of steps to move up one chaacter


    public:
        void setPins(int step_pin, int direction_pin, int enable_pin){
            stepPin = step_pin;
            directionPin = direction_pin;
            enablePin = enable_pin;
            pinMode(stepPin, OUTPUT);
            pinMode(directionPin,OUTPUT);
            pinMode(enablePin,OUTPUT);
        }

        // Loads paper into the machine
        // @params stepsPerSecond The motor speed in steps/second
        void load(int stepsPerSecond){
            step(loadSteps, stepsPerSecond);
            position = 0;
        }

        // Unloads paper from the machine
        // @params stepsPerSecond The motor speed in steps/second
        void unload(int stepsPerSecond){
            step(unloadSteps, stepsPerSecond);
        }

        // Moves the stepper to the specified character
        // @param desiredCharacter The character to go to
        // @param stepsPerSecond The speed of the motor in steps/second
        void goToCharacter(int desiredCharacter, int stepsPerSecond){

            int desiredPosition = desiredCharacter * stepsPerCharacter;

            goTo(desiredPosition, stepsPerSecond);
        }
};

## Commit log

2019-10-22 Translator passes all unit tests and split_into_lines is functioning correctly
    [translator.py]
2019-10-27 First work on firmware creating stepper class
2019-10-27 Stepper controller with working forward-back control and goTo functions
2019-10-27 Horizontal stepper class with working home and go to character methods
2019-10-27 Full servo control with both horizontal and paper stepper classes
2019-10-28 Probable implementation of 5 GCODE commands but arduino giving trouble
2019-10-28 Functions working but problems with serial, reusing serial pins suspected
    [ArduinoFirmware.ino]
2019-10-28 Potentially fixed errors by initializing classes within loop
    [ArduinoFirmware.ino]
2019-10-28 Controlling stepper successfully for a moment
2019-10-29 Works for firing at least one solenoid
2019-10-29 Working for both steppers and all 14 solenoids
2019-10-29 Add first draft of PCB
    [pcb_draft1.kicad_pcb, pcb_draft1.sch]
2019-10-29 Finish wiring for PCB First Draft
    [pcb_draft1.sch]
2019-10-29 Add GND to Mode Pins
    [pcb_draft1.sch]
2019-10-29 Add footprints to most components (need to connect drivers)
    [pcb_draft1.sch]
2019-10-29 Add custom footprint for driver
    [pcb_draft1.sch]
2019-10-29 Add custom footprint for mosfet
    [pcb_draft1.sch]
2019-10-30 Steppers move with acceleration
2019-10-30 Fixed critical errors with misdefinition fo AccelStepper class and passing copy of class instead of pointer to the interpreter
    [ArduinoFirmware.ino, Steppers-2.h]
2019-10-31 Fix misdefinition of solenoid pins - stable release with motors and solenoids working
    [ArduinoFirmware.ino]
2019-11-01 Update PCB
2019-11-06 Update PCB to add fan and thermistor (needs to be fixed)
    [pcb_draft1.sch]
2019-11-09 Set semi-accurate steps per mm and fix problem with last solenoid firing
    [ArduinoFirmware.ino, Steppers-2.h]
2019-11-09 Fix speeds and accelerations for better paper movement
    [ArduinoFirmware.ino]
2019-11-10 Add interrupt sensor to home paper
2019-11-10 Update PCB with accurate connector types
    [pcb_draft1.sch]
2019-11-10 add new netlist
    [pcb_draft1.kicad_pcb, pcb_draft1.sch]
2019-11-11 Fix x axis homing
    [ArduinoFirmware.ino, Steppers-2.h]
2019-11-12 Add footprints and finalize layout - need to add 10kohm resistors
    [pcb_draft1.sch]
2019-11-12 Attempt to fix errors in non ASCI characters
    [Steppers-2.h, bp_runner.py, translator.py]
2019-11-14 Run traces for preliminarily finished board
    [pcb_draft1.kicad_pcb, pcb_draft1.sch]
2019-11-14 So found a massive logic bug which not has to be figured out in terms of the order we get the current position and write things, but serail is working and paper is movin
    [drawable.py, page.py, translator.py]
2019-11-14 fix few unconnected pads
    [pcb_draft1.kicad_pcb]
2019-11-15 Fix silkscreen and add holes
    [pcb_draft1.kicad_pcb]
2019-11-15 Look into position errors and add notes to physical
    [physical.py]
2019-11-21 Pushing any new board stuff
    [_saved_pcb_draft1.sch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]
2019-11-21 Attempt to flip paper stepper direction
    [Steppers-2.h]
2019-11-22 Switch arduino pins for PCB
2019-12-03 swapped button port for cancel and print buttons; removedp print statements
    [interface.py]
2019-12-03 Don't be alarmed
    [_saved_pcb_draft1.sch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]
2019-12-03 Deleting so many things, so much power
2019-12-03 Add attributes to account for state changes in buttons and switches:
2019-12-04 Add simple selection of files to be printed
2019-12-05 added print statements so I know where they're coming from
2019-12-05 Add filename to print statements
2019-12-06 Add checks for buttons throuought code
2019-12-06 landing page things
2019-12-06 Work from night 0f 12-5
    [terminal-dump-12-5.txt]
2019-12-06 Make led run when error signaled
    [interface.py, physical.py]
2019-12-06 Add choices for usb printing
2019-12-09 Fixing sound switch
